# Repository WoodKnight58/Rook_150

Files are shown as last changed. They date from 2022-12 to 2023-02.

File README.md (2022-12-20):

# Rook 150



This is version 5_2B. I've printed it and like it so far.
  Quick tips:
    1. Haven't clamped the bearings and it's working well so far. 
    2. For the bed and Bottom frame, I only used the screws in the outter edges. I didn't use the ones in the dovetails but they could help in bringing the pieces together.
    3. I used one bolt for each rod end in the top.
    4. I used 2 LM8UU bearings for the Y gantry as an alternative to the longer LM8LUU either should work well
    5. I haven't tested the motor wedges but will try them out if I have belt tension issues.
    6. I printed the Carriage and motor wedges in PETG since they could get hot. ABS/ASA would be even better.

Changes from Original Rook:
  1. Linear rod only (x, y , and z)
  2. 150mm x 150mm build plate
  3. Reprap- it could replicate it's own printed parts
  4. Motors have wedges to help tension
  5. V6 hotend with 40mm x 40mm heatsink fan
  6. Bottom z limit switch has mount built into base
  7. All rods are held in plase with bolts that clamp down on them
  8. Feet are part of the base



Wanted to get my idea into CAD and add to this great community.

Integrated linear rods into motion system to replace linear rails.

Increased build area to 150mm

V2 combines the front of the upper frame with the idlers and the rear of the upper frame with the motor mounts.



V4 is cut into pieces so that it can be printed on itself

# Rook
Welcome to the DIY 3D Printer called Rook!

This is a tiny mostly 3d printed CoreXY printer with a build volume of 120x120



PLEASE NOTE THIS PRINTER IS A WORK IN PROGRESS!

The goal of this printer is to make a cheap easy to build 3D printer than can be built by anyone.

Features:

- 3D Printed Frame
- CoreXY
- Dual Lead Screws
- Only Roughly $260 USD in cost

BOM

https://docs.google.com/spreadsheets/d/1oHDEvndkkvPFOBis4atrHRHK_DMTvttFUFWDg2He6To/edit#gid=0

Videos on Youtube

Support me on Patreon
https://www.patreon.com/rolohaun

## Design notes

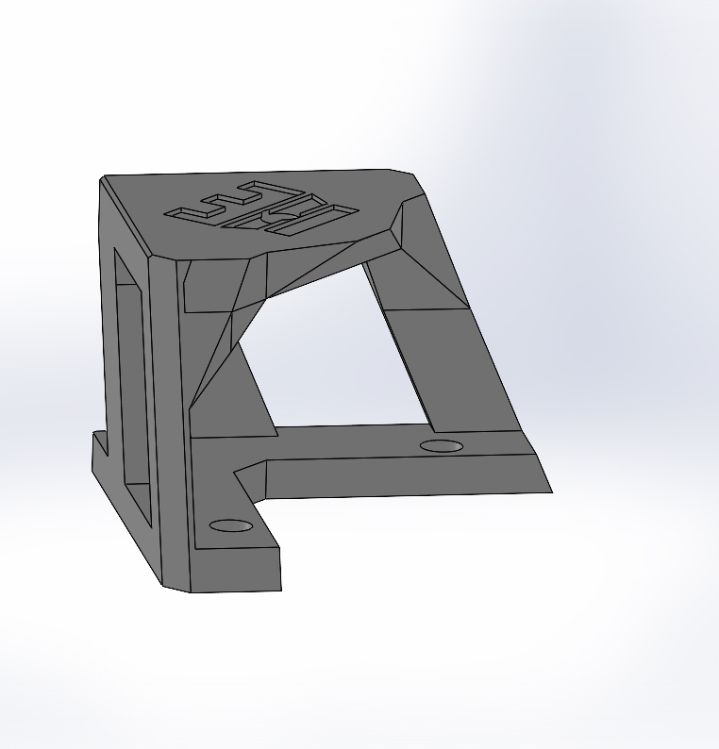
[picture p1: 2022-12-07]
CAD/Rook Foot/Foot_Mount V2.JPG

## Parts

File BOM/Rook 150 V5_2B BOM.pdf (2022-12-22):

Frame | Notes | Ali Price | AliExpress | Amazon
THERE IS NONE YOU ROOK

Motion
GT2 6mm wide Belt 3 meters | 2 Runs just over a
2 X 20T Pulley | 5mm bore, for 6mm belt | $4.99
bearings total | | $11.34 | https://www.aliexpress.com/item/33001186278.html?spm=a2g0o.order_list.0.0.21ef1802U5nwnH
meter each | $5.99 | https://www.aliexpress.com/item/902692789.html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 https://www.aliexpress.com/item/32995102911.html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,scm-url:1007.13339.291025.0,pvid:d36662fa-b085-4ded-8721-3484dd36f73a,tpp_buckets:668%232846%238109%231935&pdp_ext_f=%7B%22sku_id%22%3A%2266909277723%22%2C%22sceneId%22%3A%223339%22%7D&pdp_npi=2%40dis%21CAD%215.62%210.11%21%21%21%21%21%402101d1b516639980549727713e1a41%2166909277723%21rec
2 X MGN9C 200mm for Y | N/A | | https://www.aliexpress.com/item/1005001843434827.html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
1 X MGN9C 150mm for X | N/A | | https://www.aliexpress.com/item/1005001843434827.html?spm=a2g0o.cart.0.0.7ad738dattbgAI&mp=1
5 X Nema17 42mm Any you prefer | | $54.41 | https://www.amazon.ca/gp/product/B0B1Q51G8L/ref=ppx_yo_dt_b_asin_title_o03_s00?ie=UTF8&psc=1
8 X 8mm Linear Rod 250mm length | | $38.32 | https://www.aliexpress.com/item/4000272809625.html?spm=a2g0o.cart.0.0.370238daBRRiqb&mp=1
10 X LM8UU Bearing | | $4.61 | https://www.aliexpress.com/item/4000909626059.html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
2 X 200mm Lead Screw 2mm Pitch 8mm Lead | | $7.62 | https://www.aliexpress.com/item/32507277503.html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
4 X 32 x 22 Rubber Feet | | $9.00
5mm to 8mm shaft coupler | Could be 3d printed | $4.29 | https://www.aliexpress.us/item/2251832689038470.html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

Hardware
M3 Assorment | 10mm, 12mm,16mm, 20mm, 30mm

M2 x 10mm for z limit switch (2 pcs)

8 X M5 40mm for XY Carriage idlers (long)

6 X M5 x 30mm for front idler (Short

4 X M5 X 10mm Mounting foot mount to frame | N/A
14 X M5 Washers
Extruder
BMG Extruder Bowden | $13.00 | https://www.aliexpress.com/item/1005003423850142.html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

BED

150mm x 150mm x 3mm, 12v Heated Bed | $9.43 | https://www.aliexpress.us/item/2251832248316953.html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
Bet Leveling Screws, springs, thumbwheels | $3.70 | https://www.aliexpress.us/item/2251832709404329.html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,scm-url:1007.40050.281175.0,pvid:a805b5af-c1f7-408c-bc00-22886cfeece6,tpp_buckets:668%232846%238113%231998&pdp_ext_f=%7B%22sku_id%22%3A%2210000001843536349%22%2C%22sceneId%22%3A%2230050%22%7D&pdp_npi=2%40dis%21USD%211.25%211.09%21%21%21%21%21%40210312f816716394417581702ed428%2110000001843536349%21rec

Electronics
24v
24 Volt 6 Amp Power Supply AC Adapter | $25.99
CR-10 Style Hotend 24v ( Cheapest, but lower quality. I have had good luck with these though, I usually buy from amazon) | $8.61 | https://www.aliexpress.com/item/32925732347.html?spm=a2g0o.cart.0.0.192238daLzuFTA&mp=1
120mm 24v fan for layer cooling (Cheaper on Amazon ) | $18.00 | https://www.aliexpress.com/item/33021068426.html?spm=a2g0o.order_list.0.0.64f31802VN9NPc
3010 24v ball bearing fan for hotend ( I recommend
GDstime ) | $11 | https://www.aliexpress.com/item/1005003087542512.html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

Meanwell 24v 15a 350w

upgrade if wanting
heated bed | $40.00 | https://www.amazon.com/LRS-350-24-Switching-Supply-350-4W-115Vac/dp/B013ETVO12?th=1
150mm 24v Silicone heater | $14.71 | https://www.amazon.com/Acogedor-Silicone-Flexible-Adhesive-Thermistor/dp/B0B5V5D5FL?th=1

Not voltage Dependent

100 Brass Heated M3x5x4 | | $8.00 | https://www.aliexpress.com/item/4000232858343.html?spm=a2g0o.order_list.0.0.2ba61802mrxqNN
MKS Robin E3 v1.1 OR BTTSKR Mini E3 v3 ( More Expensive ) or SKR Pico Any mainboard should work, the Rook does use sensorless homing | | $32.00 | https://www.aliexpress.com/item/1005002618890320.html?spm=a2g0o.cart.0.0.447138daPaq61s&mp=1
Endstop Omron ( Any edstop with a similar style will work, only used for Z ) | | $4.00 | https://m.aliexpress.us/item/3256804489070551.html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
Recommended, heats up really fast, easy to mount and good quality | can get 12v or 24v | | https://www.aliexpress.com/item/1005004704341801.html?spm=a2g0o.order_list.0.0.67681802yxJymx

12v
Power Supply 12v, 10a | $21 | https://www.amazon.com/ALITOVE-100-240V-Converter-Transformer-5-5x2-1mm/dp/B07MXXXBV8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

stranded silicone wire for heated bed, stranded 20awg
V6 Hotend, all metal, 12v, bowden | $7.75 | https://www.aliexpress.us/item/3256803000529672.html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
2x 7530 12v blower fans | $10 | https://www.aliexpress.us/item/2251801505487752.html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
4010 Fan, 12v | $4 | https://www.aliexpress.us/item/3256804671765912.html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
ptfe tube, 4mm OD, 2mm ID, 1m long | $3 | https://www.aliexpress.us/item/3256801260455800.html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
Motor Wires, 50cm, xh2.54 | $5 | https://www.aliexpress.us/item/2251832624960694.html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
12v 17a 200w Meanwell ($36) | smallest for heated bed | https://www.amazon.com/MEAN-WELL-LRS-150-12-Single-Switchable/dp/B018RE4CJK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
12v 12.5a 150w Meanwell ($25) | might be too small | https://www.amazon.com/MEAN-WELL-LRS-150-12-Single-Switchable/dp/B018RE4CJK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
Tiny M 6mm bed with mains heater ($63) | don't have mounting yet | https://www.aliexpress.us/item/3256802660304098.html?gatewayAdapt=glo2usa4itemAdapt&_randl_shipto=US
Solid State Relay | Go quality
TOTAL USD | $261.44 | *doesn't include 24v

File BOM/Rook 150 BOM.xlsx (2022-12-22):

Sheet: Sheet1
Frame | Notes | Ali Price | AliExpress | Amazon
THERE IS NONE YOU ROOK
Motion
GT2 6mm wide Belt 3 meters | 2 Runs just over a meter each | $5.99 | https://www.aliexpress.com/item/902692789.html?pdp_ext_f=%7B%22sku_id%22%3A%2266484598505%22%7D
2 X 20T Pulley | 5mm bore, for 6mm belt | $4.99 | https://www.aliexpress.com/item/32995102911.html?scm_id=1007.13339.291025.0&scm-url=1007.13339.291025.0
F695 Bearing Pack of 10 you need 2 packs as you need 16 bearings total |  | $11.34 | https://www.aliexpress.com/item/33001186278.html?spm=a2g0o.order_list.0.0.21ef1802U5nwnH
2 X MGN9C 200mm for Y | N/A |  | https://www.aliexpress.com/item/1005001843434827.html?spm=a2g0o.cart.0.0.3ba738daQSzDJC&mp=1 | https://www.amazon.ca/gp/product/B09VC1RWNJ/ref=ppx_yo_dt_b_asin_title_o04_s00?ie=UTF8&th=1
1 X MGN9C 150mm for X | N/A |  | https://www.aliexpress.com/item/1005001843434827.html?spm=a2g0o.cart.0.0.7ad738dattbgAI&mp=1
5 X Nema17 42mm Any you prefer |  | $54.41 |  | https://www.amazon.ca/gp/product/B0B1Q51G8L/ref=ppx_yo_dt_b_asin_title_o03_s00?ie=UTF8&psc=1
4 X 8mm Linear Rod 250mm length |  | $38.32 | https://www.aliexpress.com/item/4000272809625.html?spm=a2g0o.cart.0.0.370238daBRRiqb&mp=1
10 X LM8UU Bearing |  | $4.61 | https://www.aliexpress.com/item/4000909626059.html?curPageLogUid=ZCqGzF8qHTlg
2 X 200mm Lead Screw 2mm Pitch 8mm Lead |  | $7.62 | https://www.aliexpress.com/item/32507277503.html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
4 X 32 x 22 Rubber Feet |  | $9.00
Hardware
M3 Assorment | 10mm, 12mm,16mm, 20mm, 30mm
M2 x 10mm for z limit switch (2 pcs)
8 X M5 40mm for XY Carriage idlers (long)
6 X M5 x 30mm for front idler (Short
4 X M5 X 10mm Mounting foot mount to frame | N/A
14 X M5 Washers
Extruder
BMG Extruder Bowden |  | $13.00 | https://www.aliexpress.com/item/1005003423850142.html?curPageLogUid=cXf0HsMSrtby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
BED
150mm x 150mm x 3mm, 12v Heated Bed |  | $9.43 | https://www.aliexpress.us/item/2251832248316953.html?curPageLogUid=TIyEBGfaB0l8
Bet Leveling Screws, springs, thumbwheels |  | $3.70 | https://www.aliexpress.us/item/2251832709404329.html?scm_id=1007.40050.281175.0&scm-url=1007.40050.281175.0
Electronics
24v
24 Volt 6 Amp Power Supply AC Adapter |  | $25.99
CR-10 Style Hotend 24v ( Cheapest, but lower quality. I have had good luck with these though, I usually buy from amazon) |  | $8.61 | https://www.aliexpress.com/item/32925732347.html?spm=a2g0o.cart.0.0.192238daLzuFTA&mp=1
120mm 24v fan for layer cooling (Cheaper on Amazon ) |  | $18.00 | https://www.aliexpress.com/item/33021068426.html?spm=a2g0o.order_list.0.0.64f31802VN9NPc
3010 24v ball bearing fan for hotend ( I recommend GDstime ) |  | $11 | https://www.aliexpress.com/item/1005003087542512.html?curPageLogUid=uvkSwRIyEizR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
Meanwell 24v 15a 350w | upgrade if wanting heated bed | $40.00 |  | https://www.amazon.com/LRS-350-24-Switching-Supply-350-4W-115Vac/dp/B013ETVO12?th=1
150mm 24v Silicone heater |  | $14.71 |  | https://www.amazon.com/Acogedor-Silicone-Flexible-Adhesive-Thermistor/dp/B0B5V5D5FL?th=1
Not voltage Dependent
100 Brass Heated M3x5x4 |  | $8.00 | https://www.aliexpress.com/item/4000232858343.html?spm=a2g0o.order_list.0.0.2ba61802mrxqNN
MKS Robin E3 v1.1 OR BTTSKR Mini E3 v3 ( More Expensive ) or SKR Pico Any mainboard should work, the Rook does use sensorless homing |  | $32.00 | https://www.aliexpress.com/item/1005002618890320.html?spm=a2g0o.cart.0.0.447138daPaq61s&mp=1
Endstop Omron ( Any edstop with a similar style will work, only used for Z ) |  | $4.00 | https://m.aliexpress.us/item/3256804489070551.html?_randl_shipto=US
Trianglelab TCHC TD6S Hotend ( TD6S Hotend B ) Recommended, heats up really fast, easy to mount and good quality | can get 12v or 24v |  | https://www.aliexpress.com/item/1005004704341801.html?spm=a2g0o.order_list.0.0.67681802yxJymx
12v
Power Supply 12v, 10a |  | $20.99 |  | https://www.amazon.com/ALITOVE-100-240V-Converter-Transformer-5-5x2-1mm/dp/B07MXXXBV8
stranded silicone wire for heated bed, stranded 20awg
V6 Hotend, all metal, 12v, bowden |  | $7.75 | https://www.aliexpress.us/item/3256803000529672.html?curPageLogUid=YKusnNdKiInV
2x 7530 12v blower fans |  | $10 | https://www.aliexpress.us/item/2251801505487752.html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
4010 Fan, 12v |  | $4 | https://www.aliexpress.us/item/3256804671765912.html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
ptfe tube, 4mm OD, 2mm ID, 1m long |  | $3 | https://www.aliexpress.us/item/3256801260455800.html?curPageLogUid=hKndlGwgQDB6
Motor Wires, 50cm, xh2.54 |  | $5 | https://www.aliexpress.us/item/2251832624960694.html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
12v 17a 200w Meanwell ($36) | smallest for heated bed |  |  | https://www.amazon.com/MEAN-WELL-LRS-150-12-Single-Switchable/dp/B018RE4CJK
12v 12.5a 150w Meanwell ($25) | might be too small |  |  | https://www.amazon.com/MEAN-WELL-LRS-150-12-Single-Switchable/dp/B018RE4CJK
Tiny M 6mm bed with mains heater ($63) | don't have mounting yet |  | https://www.aliexpress.us/item/3256802660304098.html?gatewayAdapt=glo2usa4itemAdapt&_randl_shipto=US
Solid State Relay | Go quality
TOTAL USD |  | $257.15 | *doesn't include 24v

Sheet: Sheet2
Bed alternatives
180mm bed | https://www.aliexpress.us/item/2251832818238912.html?curPageLogUid=pQQHRqNGkRQw
150mm x 6mm tiny M | https://www.aliexpress.us/item/3256804137838751.html?curPageLogUid=JTIDNAJv66Co
180 bed, magnet, bildtech, screws | https://www.aliexpress.us/item/2255800343160168.html?scm_id=1007.40050.281175.0&scm-url=1007.40050.281175.0
150mm 12v alternative | https://www.aliexpress.us/item/3256801230812850.html?scm_id=1007.40050.281175.0&scm-url=1007.40050.281175.0
180mm, 24v | https://www.aliexpress.us/item/3256801728010540.html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

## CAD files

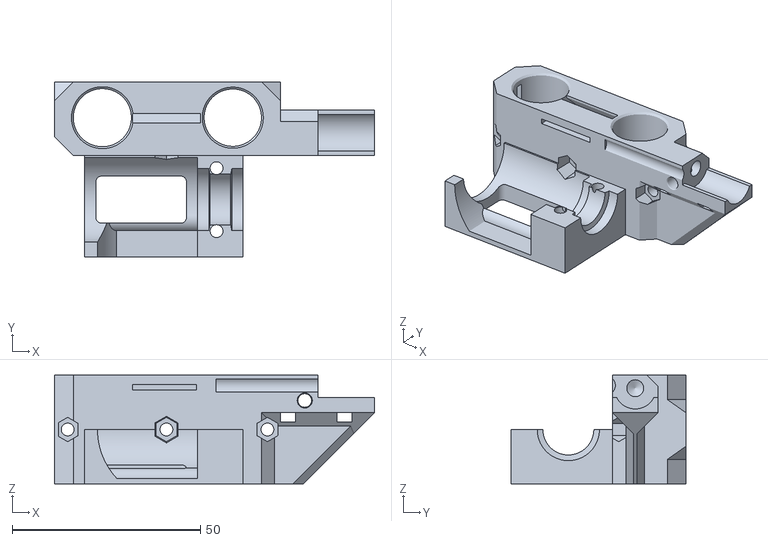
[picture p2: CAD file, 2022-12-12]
Frame/Rook 150 V5_2/Rook_150_Carriage_Main_V5_2.STL
84.9 x 46.5 x 28.9

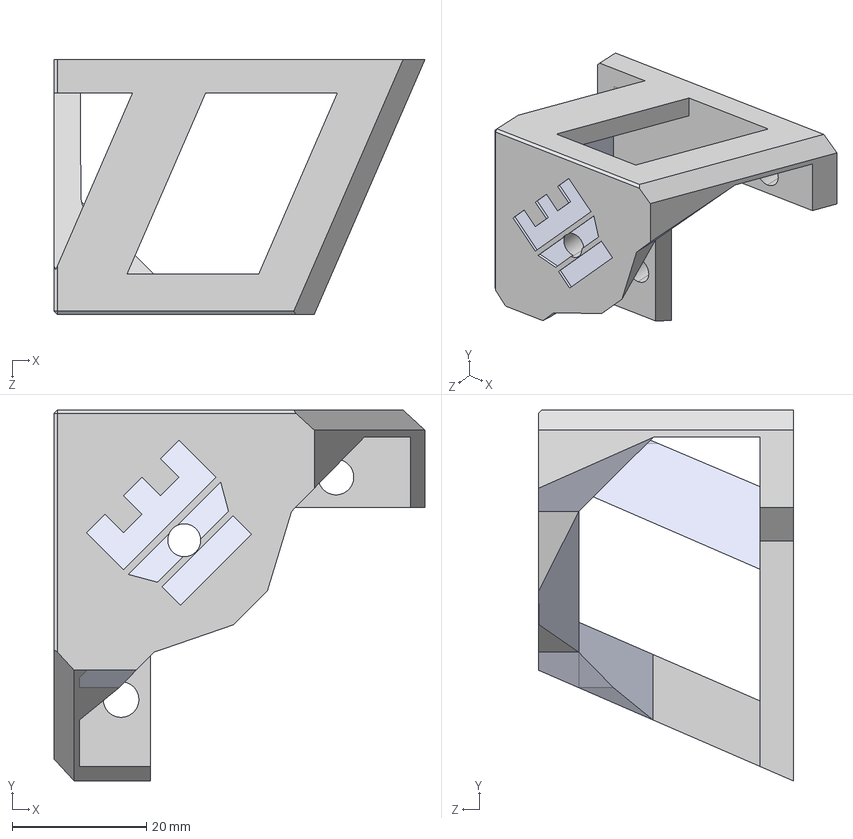
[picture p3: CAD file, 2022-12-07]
CAD/Rook Foot/Foot_Mount V3.STEP
55.3 x 55.3 x 38.0 mm

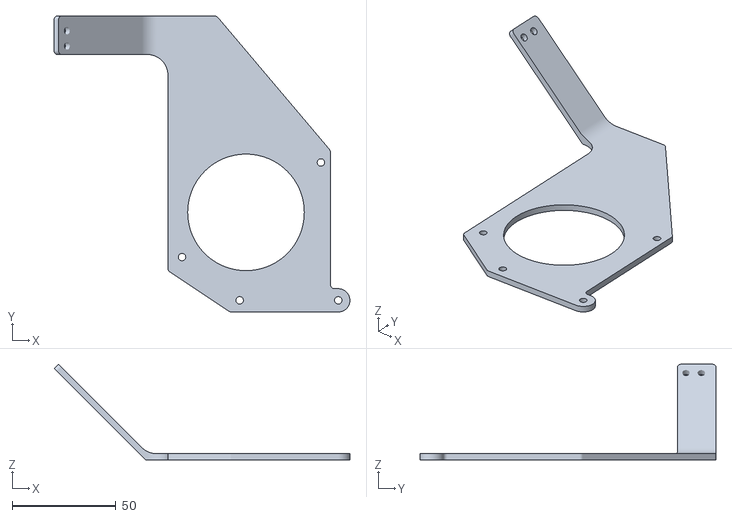
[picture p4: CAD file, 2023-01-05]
Frame/Fan/Rook_150_Fan_Support_Right_V5_2B.STL
142.9 x 143.0 x 46.2

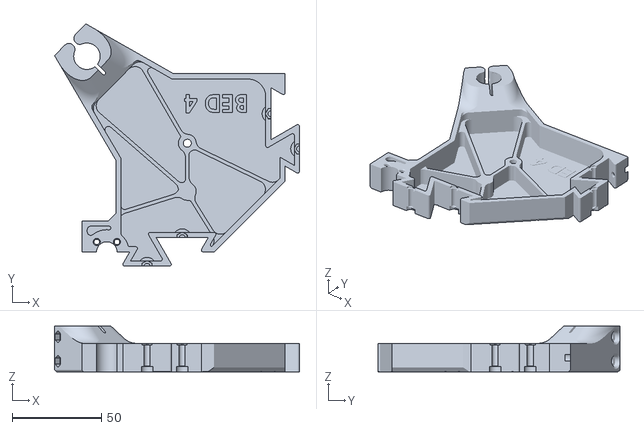
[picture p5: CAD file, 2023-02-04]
Frame/Rook 150 V5_2/Ender Pro 2 Bed/Rook_150_Bed_4_V5_2B_EnderPro2.STL
137.4 x 135.9 x 25.6

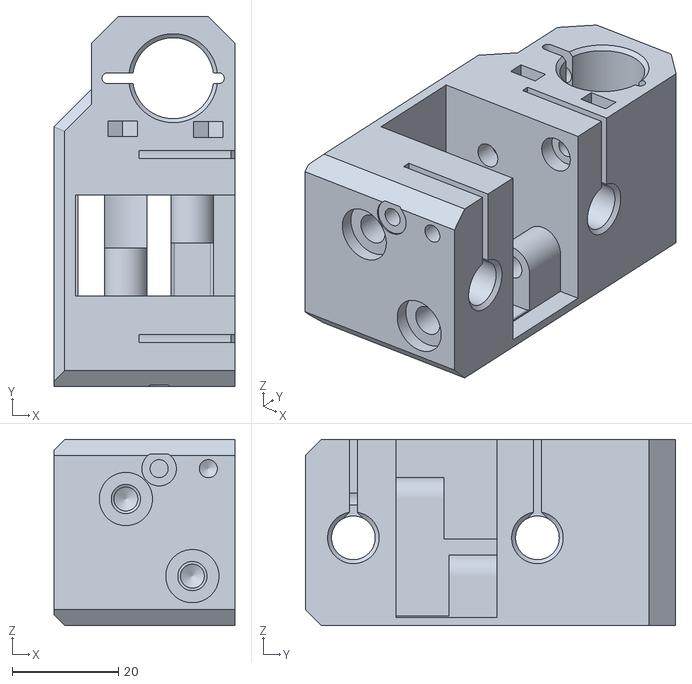
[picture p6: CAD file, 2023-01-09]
Frame/Rook 150 V5_2/Rook_150_Gantry_Right_V5_2B.STL
34.0 x 69.5 x 35.0

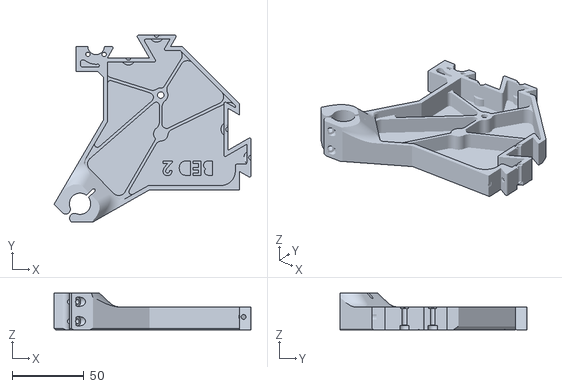
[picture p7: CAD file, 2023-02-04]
Frame/Rook 150 V5_2/Ender Pro 2 Bed/Rook_150_Bed_2_V5_2B_EnderPro2.STL
137.4 x 130.4 x 25.6

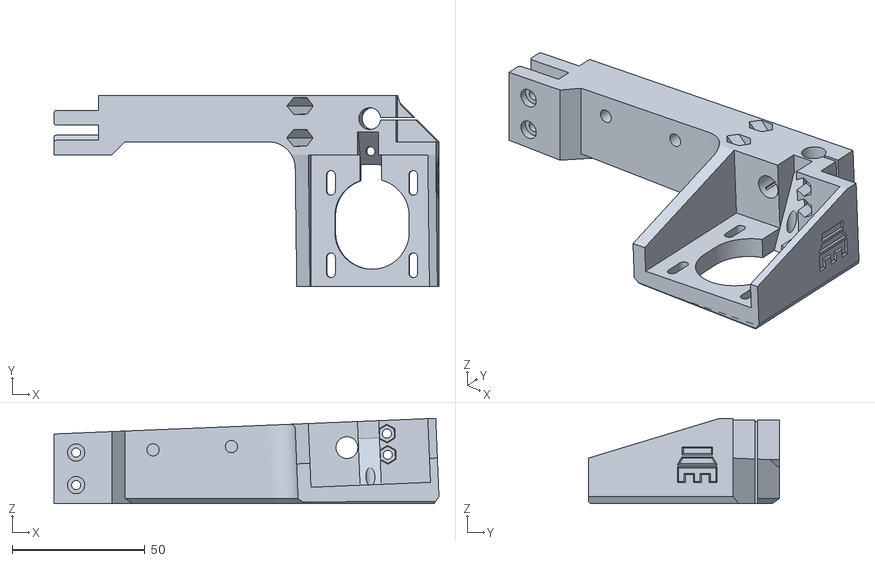
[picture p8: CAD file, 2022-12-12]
Frame/Rook 150 V5_2/Rook_150_Top_BR_V5_2.STL
144.9 x 72.0 x 32.1

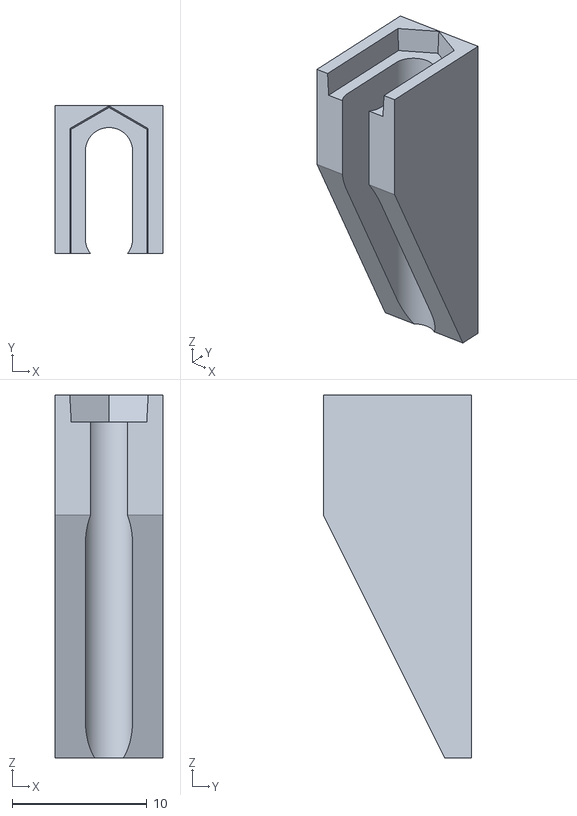
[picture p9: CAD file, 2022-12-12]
Frame/Rook 150 V5_2/Rook_150_Motor_Wedge_V5_2.STL
8.00 x 11.0 x 26.9

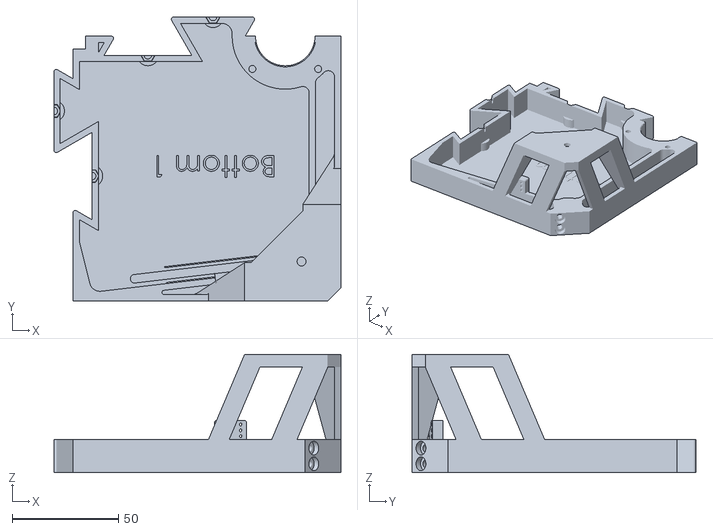
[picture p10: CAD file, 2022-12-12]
Frame/Rook 150 V5_2/Rook_150_Bottom_1_V5_2.STL
135.2 x 133.7 x 55.6

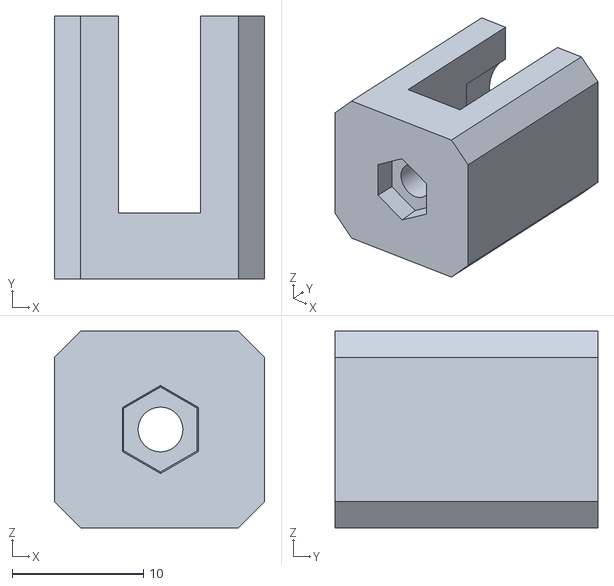
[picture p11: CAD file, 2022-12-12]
Frame/Rook 150 V5_2/Rook_150_Clip_V5_2.STL
16.0 x 20.0 x 15.0

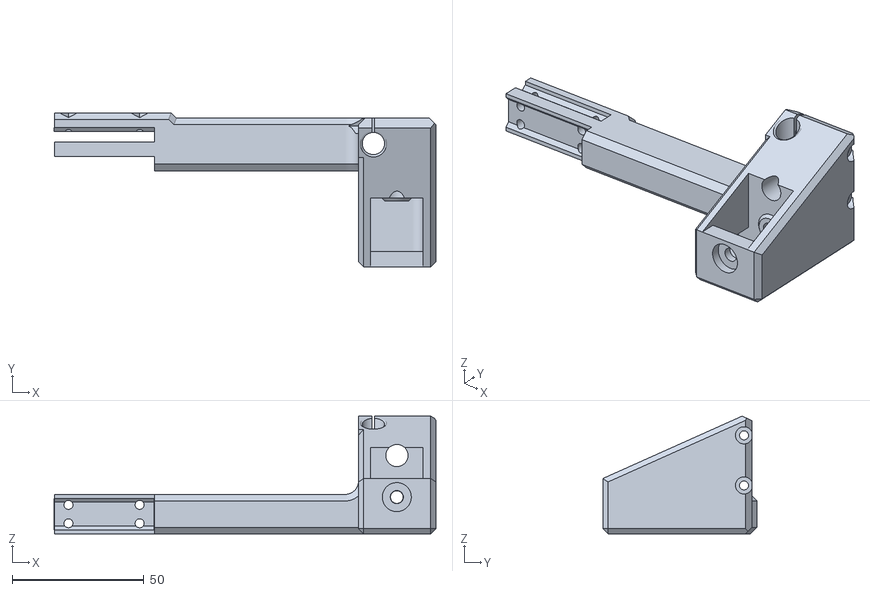
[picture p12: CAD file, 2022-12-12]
Frame/Rook 150 V5_2/Rook_150_Top_FR_V5_2.STL
145.0 x 58.6 x 44.7

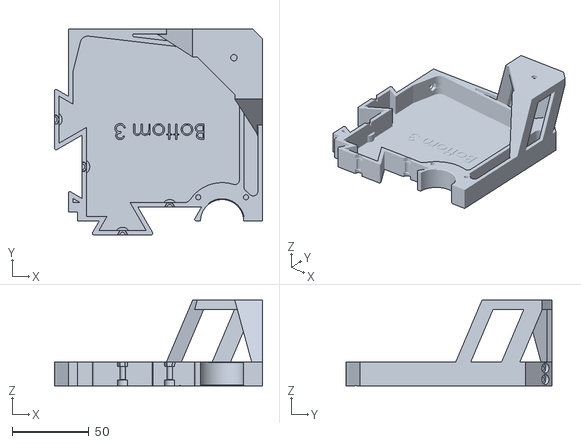
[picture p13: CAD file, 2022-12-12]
Frame/Rook 150 V5_2/Rook_150_Bottom_3_V5_2.STL
135.2 x 133.7 x 55.6

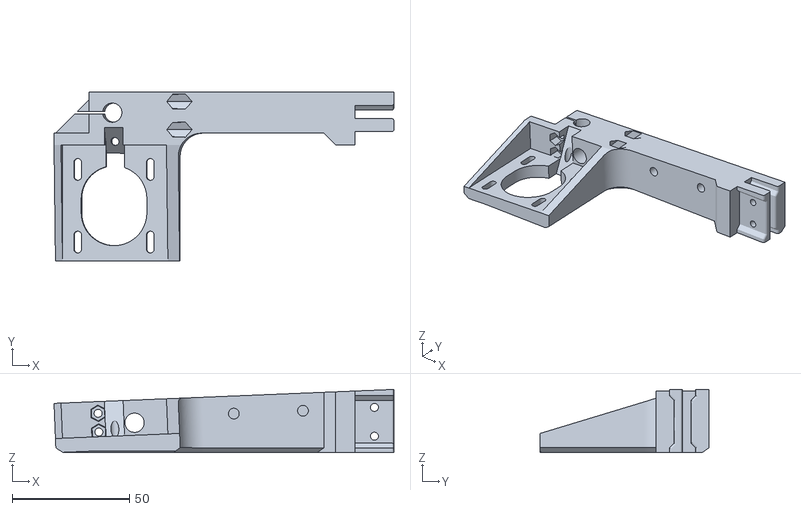
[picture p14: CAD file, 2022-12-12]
Frame/Rook 150 V5_2/Rook_150_Top_BL_V5_2.STL
145.0 x 71.9 x 26.9

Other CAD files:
Frame/Rook 150 V5_2/Rook_150_Gantry_Left_V5_2B.STL
Frame/Rook 150 V5_2/Ender Pro 2 Bed/Rook_150_Bed_1_V5_2B_EnderPro2.STL
Frame/Rook 150 V5_2/Rook_150_Bed_2_V5_2B.STL
Frame/Rook 150 V5_2/Ender Pro 2 Bed/Rook_150_Bed_3_V5_2B_EnderPro2.STL
Frame/Rook 150 V5_2/Rook_150_Bed_1_V5_2B.STL
CAD/Rook Foot/Foot_Mount V2.STEP
CAD/Rook Foot/Foot_Mount V2.STL
CAD/Rook Foot/Foot_Mount V3.STL
Frame/Rook 150 V5_1/Rook_150_Bed_1_V5_1.STL
Frame/Rook 150 V5_1/Rook_150_Bed_2_V5_1.STL
Frame/Rook 150 V5_1/Rook_150_Bed_3_V5_1.STL
Frame/Rook 150 V5_1/Rook_150_Bed_4_V5_1.STL
Frame/Rook 150 V5_1/Rook_150_Bottom_1_V5_1.STL
Frame/Rook 150 V5_1/Rook_150_Bottom_2_V5_1.STL
Frame/Rook 150 V5_1/Rook_150_Bottom_3_V5_1.STL
Frame/Rook 150 V5_1/Rook_150_Bottom_4_V5_1.STL
Frame/Rook 150 V5_1/Rook_150_Carriage_Belt_V5_1.STL
Frame/Rook 150 V5_1/Rook_150_Carriage_Fan_V5_1.STL
Frame/Rook 150 V5_1/Rook_150_Carriage_Main_V5_1.STL
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

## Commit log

2022-11-21 Cleaned up some leftover holes
2022-12-01 150mm Rook that can print itself
2022-12-07 Added 11mm clearance
    Added 11mm clearance for the bolt head in the center
    [Foot_Mount V3.STEP, Foot_Mount V3.STL]
2022-12-09 Model Ready for testing
    I'm planning on printing this out and testing it.
2022-12-09 STLs for V5_1
    [Rook_150_Bed_1_V5_1.STL, Rook_150_Bed_2_V5_1.STL, Rook_150_Bed_3_V5_1.STL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]
2022-12-12 Cleaned up the model after printing
    Cleaned up some edges and fits. Adjusted to use shorter M3 screws. Mainly 16mm and 20mm
2022-12-12 Improved STLs
    I've printed and assembled V5_1. I made some changes as I went and fixed some things I didn't like . Also tried to make the required screws more standard (M3 16mm and 20mm)
    [Rook_150_Bed_1_V5_2.STL, Rook_150_Bed_2_V5_2.STL, Rook_150_Bed_3_V5_2.STL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]
2022-12-20 Hitting motor
    Removed and added a B version to prevent it hitting the motor.
    [Rook_150_Bed_1_V5_2.STL]
2022-12-20 Replaced with B
    Removed and replaced with B version due to it hitting motor
    [Rook_150_Bed_2_V5_2.STL]
2022-12-20 Removed and replaced
    Replaced with B version since it wasn't stopping the belts from moving.
    [Rook_150_Carriage_Belt_V5_2.STL]
2022-12-20 Added B Versions
    Added B versions of bed to prevent them rubbing on the motors and B version of carriage belt clamp that stops the belt.
    [Rook_150_Bed_1_V5_2B.STL, Rook_150_Bed_2_V5_2B.STL, Rook_150_Carriage_Belt_V5_2B.STL]
2022-12-22 Added Rook 150 BOM
    [Rook 150 BOM.xlsx]
2022-12-22 Fixed number of rods
    Only had 4 listed, requires 8
    [Rook 150 BOM.xlsx]
2022-12-22 Added shaft coupler
    Third times the charm. Added shaft couplers for the lead screws.
    [Rook 150 BOM.xlsx]
2022-12-31 Includes updates from after I printed it
2023-01-05 Mount for 7530 Fan
    [Rook_150_Carriage_Belt_V5_2B.STL]
2023-01-05 Files for 7530 fan mount
    [Rook_150_Carriage_Belt_V5_2B.STL]
2023-01-05 Part Cooling Fan Mount
    Mount for 7530 fan for cooling. Can be mirrored for dual fan cooling!
    [Rook_150_Fan_Support_Right_V5_2B.STL]
2023-01-09 Delete Rook_150_Gantry_Left_V5_2.STL
    One of the nut slots was out of place.
    [Rook_150_Gantry_Left_V5_2.STL]
2023-01-09 Delete Rook_150_Gantry_Right_V5_2.STL
    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
    [Rook_150_Gantry_Right_V5_2.STL]
2023-01-09 Fixed Gantry Sides
    One of the nut slots was out of place. Updated
    [Rook_150_Gantry_Left_V5_2B.STL, Rook_150_Gantry_Right_V5_2B.STL]
2023-01-09 Updated
    Added the update gantry and part cooling fan.
